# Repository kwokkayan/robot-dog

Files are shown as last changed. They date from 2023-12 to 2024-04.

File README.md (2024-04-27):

# 23/24 COMP4601 Final Year Project

## Group information

- group: fyp23005
- title: Intelligent robot design and implementation

## File Structure

- `3D_model`: STL and blender files
- `docker`: docker files for development and production environments
- `workspaces/esp32_champ_dog`: new firmware for champ
- `workspaces/newviz`: React web application for live visualizations
- `workspaces/ros/noetic`: ROS1 packages including CHAMP
- `workspaces/ros/humble`: ROS2 packages including CV utilities

## Requirements

1. `docker`, `docker-compose`, and [`docker-buildx-plugin`](https://github.com/docker/buildx)
2. Alternatively, ROS melodic to run `workspaces/ros/noetic` and ROS humble to run others.
3. `nodejs` > 21.0.0
4. Hardware requirements:
   - ESP32 microcontroller
   - MPU-9250
   - PCA9685 PWM controller
   - 12 PWM servos (MG996R, MG958, TD81XXG series...)
   - Nvidia Jetson Orin Nano Developer Kit
     - Jetpack 5.1.3
     - CUDA 11.4
   - Intel Realsense D435i

## How to run

### Firmware

1. Use PlatformIO to open `esp32_champ_dog`
2. Build and flash the firmware to `esp32`
3. Refer to `README.md` in `esp32_champ_dog` for further information.

### Development: CHAMP with ROS Melodic

1. Configure `docker-compose.yml`:
   - Web GUI Resoulution is set in `docker-compose.yml`. Please refer to [base image](https://hub.docker.com/r/dorowu/ubuntu-desktop-lxde-vnc/) for detailed configuration.
   - Pass device files to the container in `docker-compose.yml` under `device`:
     - joystick: e.g. `/dev/input/js0:/dev/input/js`
     - rfcomm socket: e.g. `/dev/rfcomm1:/dev/ttyUSB0`
     - usb socket: e.g. `/dev/ttyUSB0:/dev/ttyUSB0`
   - The following ports are opened:
     - 22: ssh
     - 5900: vnc
     - 6080: vnc
     - 9090: websocket
     - 11311, 11411: ros serial TCP socket
   - Uncomment `bind volumne` for live development
2. Run `docker-compose up -d`.
   - Use `http://localhost:6080` to access the web GUI.
   - CHAMP and other packages is installed and built
3. Refer to `README.md` in `workspaces/ros/noetic` for further information.

### Development: React webapp

1. `cd workspaces/newviz`
2. `npm i`: install dependencies
3. Configure `.env`:
   - VITE_ROS_PACKAGE=public
   - VITE_URDF_PATH=public/quadruped.urdf
   - VITE_WS_URL=`websocket url for middleware`
   - VITE_CAMERA_STREAM_URL=`http url for video stream`
4. `npm run dev`: start web server
5. Refer to `README.md` in `workspaces/newviz` for further information.

### Production environments

Start the docker container for running ROS noetic packages

```bash
$ cd docker/
$ ./build.sh noetic
$ ./run.sh noetic
> roslaunch test_config bringup.launch
```

Start the docker container for running ROS1-to-ROS2 bridge

```bash
$ cd docker/
$ ./build.sh bridge
$ ./run.sh bridge
> ros2 run ros1_bridge dynamic_bridge 2>/dev/null
```

Start the docker container for running ROS humble packages (Note that the building process of ROS packages is started after starting the container as host CUDA library are required)

```bash
$ cd docker/
$ ./build.sh humble
$ ./run.sh humble
> source /opt/ros/humble/setup.bash && colcon build --symlink-install
> source install/setup.bash && ros2 launch nvblox_examples_bringup realsense_nav2_example.launch.py
```

Start the docker container for running the web dashboard (Please refer to the `README.md` in `workspaces/newviz` for getting a Firebase API key)

```bash
$ vim workspaces/newviz/.env # To configure VITE_FIREBASE_API_KEY
$ cd docker/
$ ./build.sh newviz
$ docker run --rm -p 127.0.0.1:8080:80 ros_custom-newviz-$(uname -m)
```

Then, you can access the web dashboard at `http://127.0.0.1:8080/`.

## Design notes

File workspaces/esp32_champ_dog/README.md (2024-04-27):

# ESP32_CHAMP_DOG
## File Structure
- `include`: header files and macro configs
    - `Config.h`: choose the protocol for ROS serial (Wifi, Bluetooth SSP, and Serial are available)
- `lib`: custom libraries
    - `mpu_9250`: IMU wrapper class
    - `pwm_servo`: PWM servo wrapper class
        - `pwm_servo_offset.h`: put joint offsets after calibration here
- `src`: main files
    - `BluetoothSerial.cpp`: configure TX/RX queue sizes
    - `main.cpp`: main firmware
## How to run
1. Choose the protocol used in `Config.h`:
    - Uncomment `#define ENABLE_WIFI` to enable wifi
    - Uncomment `#define USE_BLUETOOTH` to enable bluetooth
    - Comment both to use Serial
2. Configure ros serial buffers (`ros.h`)and bluetooth buffers (`BluetoothSerial.cpp`)
3. Using Platform IO, build and flash.
4. Calibrate joints using calibration mode and adjust offsets in `pwm_servo_offset.h`
## Dependencies
- `frankjoshua/Rosserial Arduino Library@^0.9.1`
- `adafruit/Adafruit PWM Servo Driver Library@^3.0.1`
- `Wire`
- `SPI`
- `kwokkayan/SparkFun MPU-9250 Digital Motion Processing (DMP) Arduino Library (For ESP32)@^1.0.1`: forked from [here](https://github.com/sparkfun/SparkFun_MPU-9250-DMP_Arduino_Library)
## Bluetooth commands
- `sudo hcitool cc <MAC>`
- `sudo hcitool auth <MAC>`
- `sudo rfcomm bind rfcomm1 <MAC>`
- `sudo rfcomm connect /dev/rfcomm1 <MAC> 1`
## How to get absoulte orientation
1. Before powering on, face the robot to the EAST to calibrate to ENU coordinates.

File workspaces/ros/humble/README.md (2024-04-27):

# ROS Humble packages

## File Structure

- `imu_tools`: provides madgwick filter to fuse IMU sensor data into an orientation
- `isaac_ros_common`: provides common packages and utilities in Isaac ROS
- `isaac_ros_image_segmentation`: provides image segmentation packages
- `isaac_ros_nvblox`: provides Nvblox, a 3D scene reconstruction package
- `isaac_ros_object_detection`: provides object detection packages (e.g., YOLO)
- `m-explore`: provides frontier exploration and map merging packages
- `pose_estimation_filter`: provides human pose estimation package for dynamic object following
- `realsense-ros`: provides ROS wrapper for Intel RealSense camera

## How to run

- Base mode: `ros2 launch nvblox_examples_bringup realsense_nav2_example.launch.py`
- Run frontier exploration node: `ros2 launch explore_lite explore.launch.py`
- Run dynamic object following node: `ros2 run pose_estimation_filter evaluator`
  - Please see [isaac_ros_unet - Quickstart](https://nvidia-isaac-ros.github.io/repositories_and_packages/isaac_ros_image_segmentation/isaac_ros_unet/index.html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) to configure and start the image segmentation node

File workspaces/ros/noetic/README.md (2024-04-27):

# ROS Noetic packages

## File Structure

- `champ*`: CHAMP files, refer to [here](https://github.com/chvmp/champ) for instructions.
- `champ_setup_assistant`: refer to [here](https://github.com/chvmp/champ_setup_assistant) for instructions.
- `champ_teleop`: refer [here](https://github.com/chvmp/champ_teleop) for instructions.
- `esp32_ros_confollers`: `ros_control` package for esp32 hardware.
- `realsense2_description`: URDF and meshs for Intel realsense cameras.
- `test_config`: main config for robot:
  - `urdf`: URDF files and meshes for the robot
  - `config`: configuration files for gait, pid, ...
  - `launch`: launch files

## How to run

- Joint calibration mode: `roslaunch test_config bringup.launch rviz:=true hardware_connected:=true publish_joint_control:=false calibrate_joints:=true balance_mode:=false`
- Hardware connected without balance mode: `roslaunch test_config bringup.launch hardware_connected:=true balance_mode:=false`
- Hardware connected with balance mode: `roslaunch test_config bringup.launch hardware_connected:=true`
- Hardware connected (TCP protocol) with balance mode: `roslaunch test_config bringup.launch hardware_connected:=true ros_serial_tcp:=true`
- Hardware connected with custom baud rate and device file: `roslaunch test_config bringup.launch hardware_connected:=true baud_rate:=1000000 device_file:=/dev/ttyUSB0`
- Joystick control:`roslaunch champ_teleop teleop.launch joy:=true`
- Refer to CHAMP for other commands

## Configuration

- Balance Mode pid: go to `src/test_config/config/pid/pid.yaml`
- Gait config: go to `src/test_config/config/gait/gait.yaml`

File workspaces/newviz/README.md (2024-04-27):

# NEWVIZ

## Prerequisite

1. Google account (for creating Firebase projects)

## Configuration

Configure [environement file] (.env):

- VITE_ROS_PACKAGE=public
- VITE_URDF_PATH=public/quadruped.urdf
- VITE_WS_URL= Websocket URL for ROS connection
- VITE_CAMERA_STREAM_URL= URL for live camera stream
- VITE_FIREBASE_API_KEY = API key of your firebase project

## Launch the Web

1. run shell command to install dependencies\
   `npm i`
2. run shell command to start web server\
   `npm run dev`

## How to get the API key

1. Visit [Firebase](https://firebase.google.com/) and go to console
2. Create a new Firebase project
3. Go to Project Setting and create a web app
4. Firebase will generate API key, appId for you
5. Replace the codes in firebase.js with your web app's Firebase configuration
   (See [Add Firebase to your JavaScript project](https://firebase.google.com/docs/web/setup#add_firebase_to_your_app) )

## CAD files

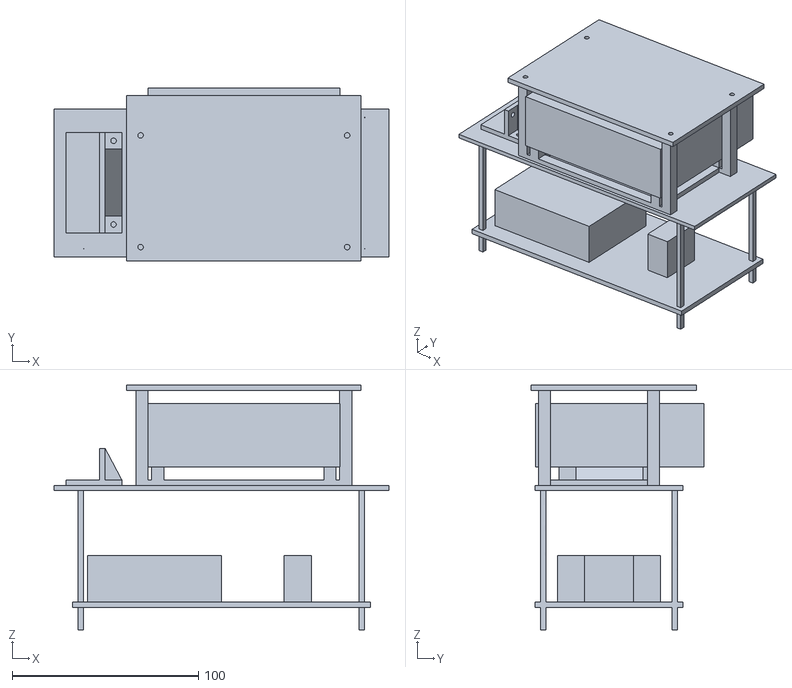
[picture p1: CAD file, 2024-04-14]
3D_model/stl_models/tower.stl
180.0 x 93.0 x 131.5

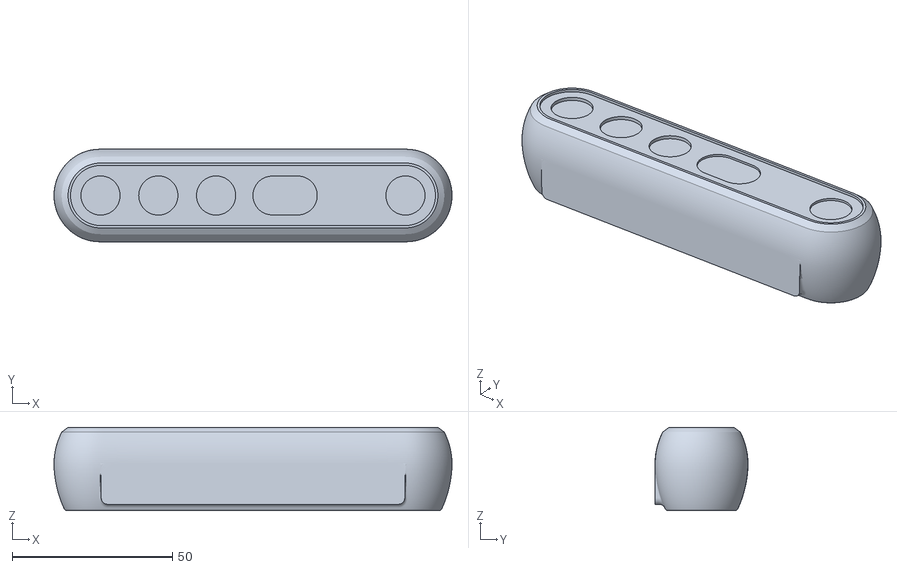
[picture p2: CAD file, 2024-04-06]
workspaces/newviz/public/realsense2_description/meshes/d455.stl
124.0 x 29.0 x 26.0

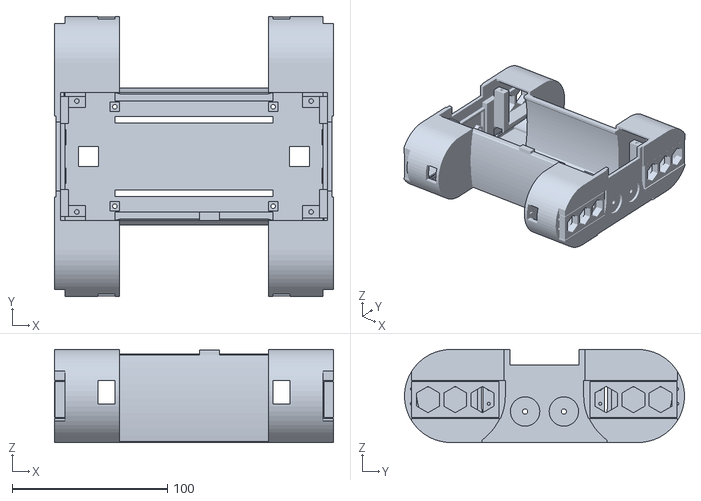
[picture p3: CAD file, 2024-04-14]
workspaces/newviz/public/test_config/meshes/base.stl
180.0 x 180.5 x 60.0

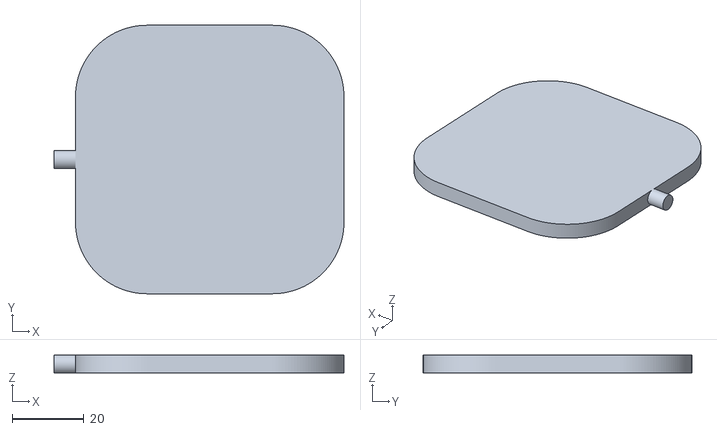
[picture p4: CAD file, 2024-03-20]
workspaces/ros/noetic/champ_description/meshes/arm/wrist2.stl
81.0 x 75.0 x 5.00

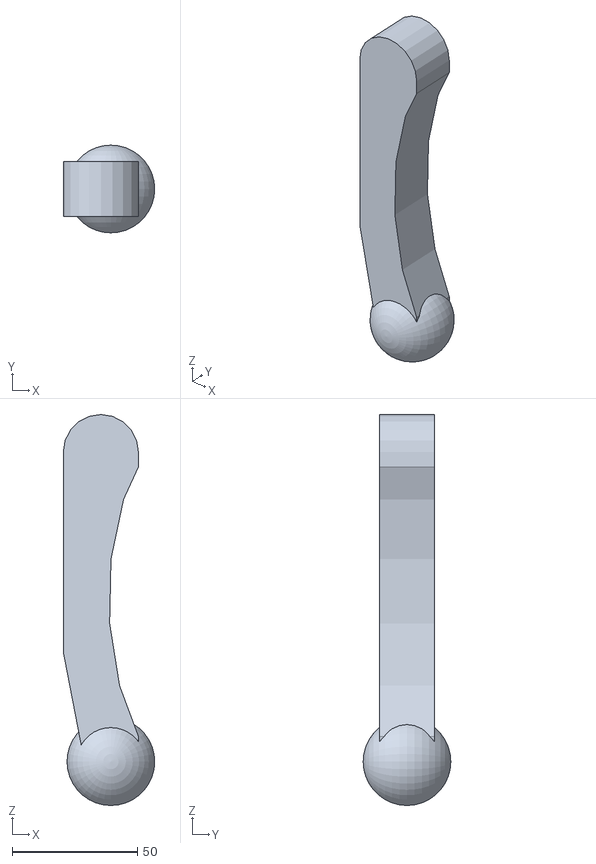
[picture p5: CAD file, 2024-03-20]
workspaces/ros/noetic/champ_description/meshes/lower_leg.stl
36.5 x 35.0 x 156.0

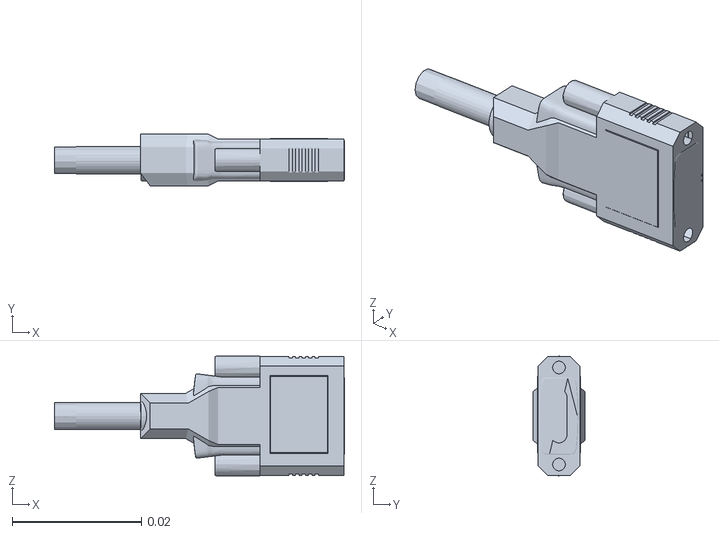
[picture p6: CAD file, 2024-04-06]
workspaces/ros/noetic/realsense2_description/meshes/plug.stl
0.0448 x 0.008 x 0.0185

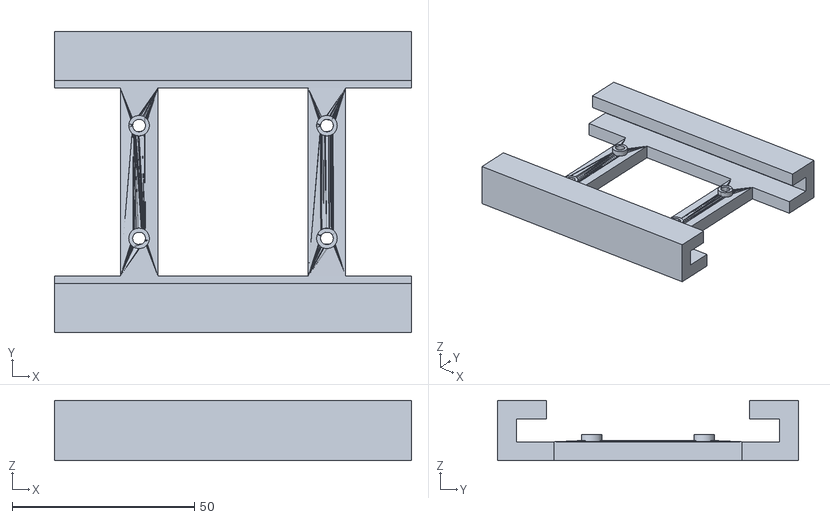
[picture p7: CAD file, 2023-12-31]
3D_model/stl_models/refined_sbc_header.stl
97.8 x 82.4 x 16.5

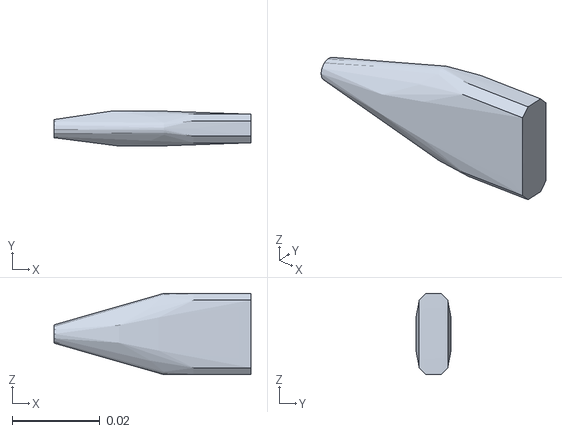
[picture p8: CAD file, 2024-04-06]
workspaces/newviz/public/realsense2_description/meshes/plug_collision.stl
0.0448 x 0.008 x 0.0185

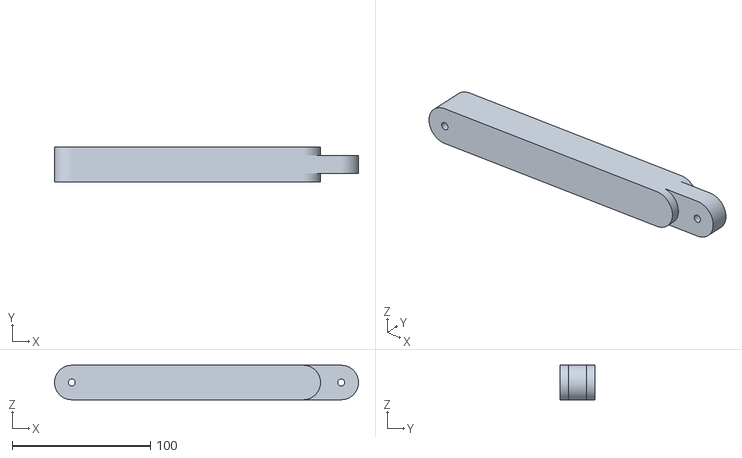
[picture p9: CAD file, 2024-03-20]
workspaces/ros/noetic/champ_description/meshes/arm/lower_arm.stl
220.0 x 25.0 x 25.0

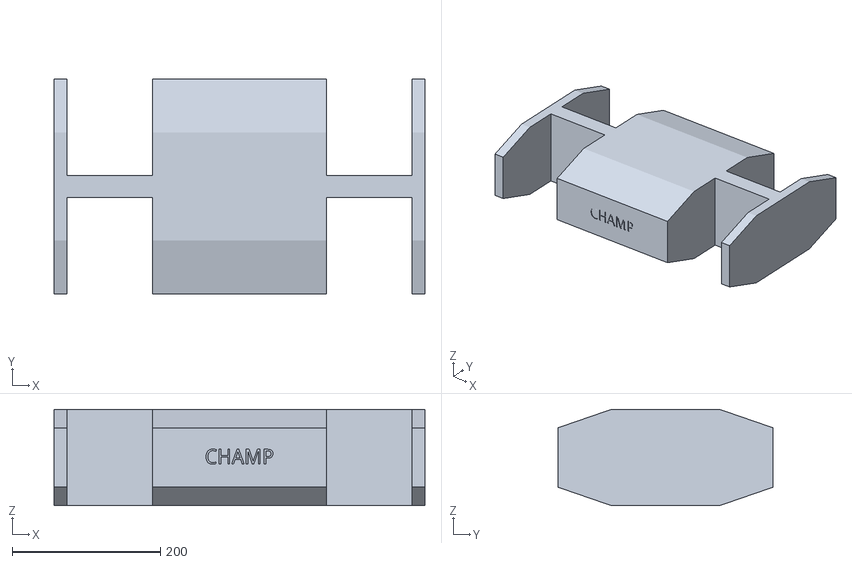
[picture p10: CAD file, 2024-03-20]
workspaces/ros/noetic/champ_description/meshes/base.stl
500.0 x 290.0 x 130.0

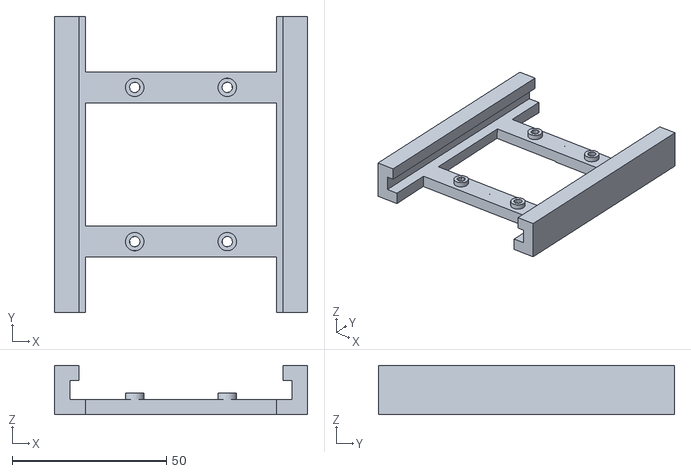
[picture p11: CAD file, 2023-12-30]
3D_model/stl_models/small_sbc_header.stl
82.0 x 96.0 x 16.0

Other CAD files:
workspaces/newviz/public/test_config/meshes/tower.stl
workspaces/ros/noetic/test_config/meshes/tower.stl
3D_model/blends/base.blend
3D_model/blends/bumper.blend
3D_model/blends/foot.blend
3D_model/blends/hip.blend
3D_model/blends/lower-leg.blend
3D_model/blends/tower.blend
3D_model/blends/upper-leg.blend
3D_model/stl_models/body-bottom.stl
3D_model/stl_models/body-bumper.stl
3D_model/stl_models/body-top.stl
3D_model/stl_models/lower-joint_foot_left.stl
3D_model/stl_models/lower-joint_foot_right.stl
3D_model/stl_models/lower-joint_left_leg.stl
3D_model/stl_models/lower-joint_right_leg.stl
3D_model/stl_models/servo-arm-extension.stl
3D_model/stl_models/shoulder_join_left.stl
3D_model/stl_models/shoulder_join_right.stl
3D_model/stl_models/triangular_ruler.stl
3D_model/stl_models/upper-joint_left1.stl
3D_model/stl_models/upper-joint_left2.stl
3D_model/stl_models/upper-joint_right1.stl
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

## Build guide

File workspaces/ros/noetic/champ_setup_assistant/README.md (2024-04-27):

# CHAMP Setup Assistant  
This software auto generates a configuration package containing all the [files](https://github.com/chvmp/champ_setup_assistant/tree/master/templates) necessary to make CHAMP walk. 

CHAMP Setup Assistant
## 1. Installation

### 1.1. Clone and install all dependencies:

        sudo apt install -y python-rosdep
        cd <your_ws>/src
        git clone https://github.com/chvmp/champ_setup_assistant
        cd ..
        rosdep install --from-paths src --ignore-src -r -y

### 1.2.  Build your workspace:

        cd <your_ws>
        catkin_make
        source <your_ws/>/devel/setup.bash

## 2. Quick Start

### 2.1. Run the setup assistant:

        roslaunch champ_setup_assistant setup_assistant.launch 

Configure your robot by loading a URDF or manually key in the configuration parameters. If you don't have a URDF now, you can download [ANYmal](https://github.com/chvmp/anymal_b_simple_description/tree/master/urdf) or [SpotMicro](https://github.com/chvmp/spotmicro_description/blob/master/urdf/spotmicroai.urdf) to try the package.

## 3. Leg Configuration

You can either use a URDF file or manually key in the origin of each actuator in the robot.

### 3.1. Using a URDF file:

 3.1.1 The following assumptions have been made to avoid fragmentation across different robots as there can be thousands of ways to create a robot's URDF. You need to modify your URDF if any of these assumptions are not met:

- There are no rotation between frames (joint's origin-rpy are all set to zero).
- Hip joints rotate in the X axis.
- Upper Leg joints rotate in the Y axis.
- Lower Leg joints rotate in the Y axis.
- Origins of actuators' meshes are located at the center of rotation.
- All joints at zero position will results the robot's legs to be fully stretched towards the ground. From frontal and sagittal view, all legs should be perpendicular to the ground.

You can use the image below as a reference.

AXES: +X: Red, +Y: Green, +Z: Blue 
  CHAMP Setup Assistant

3.1.2 Load the URDF file:
   
- Click the 'BROWSE URDF' button on the upper right corner and click the URDF file you want to use from the file browser. Double click the file or click 'Open' to load the URDF.

- Click the 'LOAD' button. This will list down the links of the robot on the left pane and display the robot's meshes on the RVIZ widget. Take note that it may take a while for huge mesh files to load.

    CHAMP Setup Assistant

3.1.3 Select the namespace for each leg (auto-configuration):
   
- Select the correct namespace for each leg on the drop-down menu. 

  CHAMP Setup Assistant

  This namespace is the unique identifier used by the URDF's author to differentiate each leg. For instance, Anymal's hip links are named as LF_HIP (front left), LH_HIP (rear left), RF_HIP (right front), RH_HIP (rear right). The assistant will parse the namespaces as LF_, LH_, RF_, and RH_. After selecting the namespaces for all the legs, the assistant will automatically drag the links to its respective leg parts, emptying the left pane.

3.1.4 Manually adding links if auto-configuration in previous step (3.1.2) fails:

- You can also add a link to each leg part manually by clicking on a leg tab (ie 'Left Front Leg'). Select a link on the left pane and click '>' to add. This would be useful if the assistant fails to parse the namespaces.
   
  CHAMP Setup Assistant

3.1.5 Verify the configuration:

- To visualize a configured link for a leg part, click on one of the leg tabs (ie 'Left Front Leg') and select the part. The link should now be highlighted on the RVIZ widget. Check all the leg tabs if the configuration is correct.

  CHAMP Setup Assistant

### 3.2. Manual Joint Configuration:

This step is only required if you don't have a URDF file to use. In this step, you'll define the position of each actuator in your robot to help the controller find the relative position of each joints.

- Click the 'Left Front Leg' tab and key in the position for each actuator. When defining an actuator's position, x, y, and z refers to:

  x: Translation in the x axis from a reference frame. + x to the front, -x to the back.

  y: Translation in the y axis from a reference frame. + y to the left, -y to the right.

  z: Translation in the z axis from a reference frame. + z up, -z down.

By reference frame, it means the previous part in this chain: base - hip - upper_leg - lower_leg - foot. For instance if you're defining the position of the actuator at the hip, the reference frame will be 'base' and if youre defining the position of the upper_leg then your reference frame will be 'hip'.  

You can take a look at the diagram below to gain some intuition. Alway define these positions from a bird's eye view.
   
CHAMP Setup Assistant

Some axis won't allow you to define in a certain direction if the assistant thinks that it doesn't make sense to define the position towards that direction. For instance, you won't be able to define front right hip's actuator y value as positive as this actuator is always at the right side (-y) of the base.

Once you're done with the left-front leg, the assistant will somehow predict the rest of the actuators' position. You can click on the rest of the leg tabs to check if the predictions are correct. You can still define the position manually if the prediction is wrong.

## 4. Gait Configuration

Click on the 'Gait Configuration' tab to define the robot's walking parameters.

CHAMP Setup Assistant

  - **Knee Orientation** - How the knees should be bent. You can can configure the robot to follow the following orientation .>> .>< .<< .<> where dot is the front side of the robot.

  - **Max Linear Velocity X** (meters/second) - Robot's maximum forward/reverse speed.

  - **Max Linear Velocity Y** (meteres/second) - Robot's maximum speed when moving sideways.

  - **Max Angular Velocity Z** (radians/second)- Robot's maximum rotational speed.

  - **Stance Duration** (seconds)- How long should each leg spend on the ground while walking. You can set this to default(0.25) if you're not sure. The higher the stance duration the further the displacement is from the reference point.

  - **Leg Swing Height** (meters)- Trajectory height during swing phase.

  - **Leg Stance Height** (meters)- Trajectory depth during stance phase.

  - **Robot Walking Height** (meters) - Distance from hip to the ground while walking. Take note that setting this parameter too high can get your robot unstable.

  - **CoM X Translation** (meters) - You can use this parameter to move the reference point in the X axis. This is useful when you want to compensate for the weight if the center of mass is not in the middle of the robot (from front hip to rear hip). For instance, if you find that the robot is heavier at the back, you'll set a negative value to shift the reference point to the back.

  - **Odometry Scaler** - You can use this parameter as a multiplier to the calculated velocities for dead reckoning. This can be useful to compensate odometry errors on open-loop systems. Normally this value ranges from 1.0 to 1.20.
  
## 5. Generate Config Package

  Before you generate the configuration package make sure you have configured all the legs and set the correct gait configurations.

- Click the 'Generate Config' tab and key-in the robot name. 
- Click the 'Browse' button to choose the 'src' directory of your current catkin workspace.
- Click 'Generate' button to create the configuration package.

  CHAMP Setup Assistant

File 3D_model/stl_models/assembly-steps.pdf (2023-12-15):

# Assembling Step

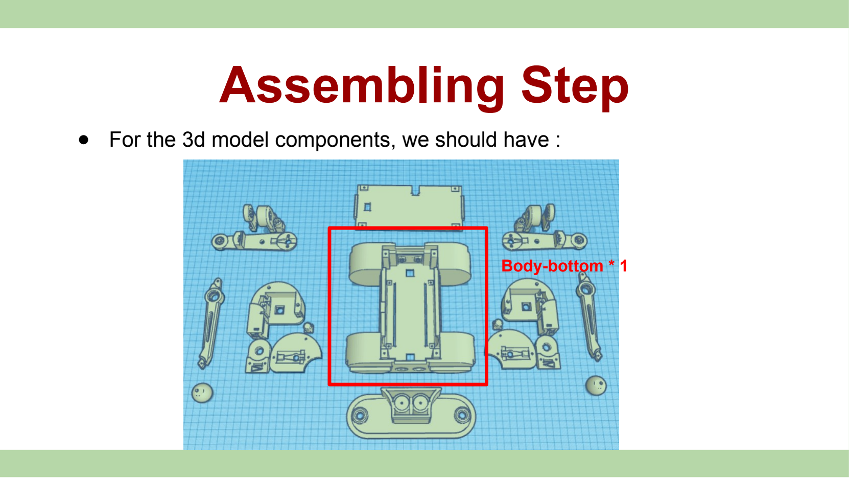
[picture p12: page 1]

- For the 3d model components, we should have :

Body-bottom * 1

Body-top * 1

Body-bumper * 2

Left-shoulder-joint * 2

Left-upper-joint * 2

Left-lower-joint * 2

Left-foot * 2

Right-shoulder-joint * 2

Right-upper-joint * 2

Right-lower-joint * 2

Right-foot * 2

# Assemble Step

- For the other components, we have :

Servo motor * 12

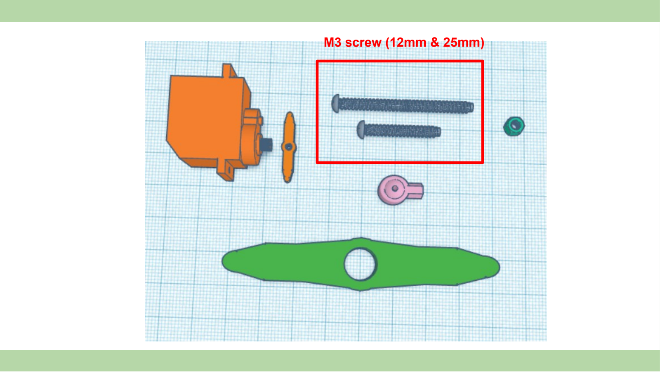
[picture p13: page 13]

M3 screw (12mm & 25mm)

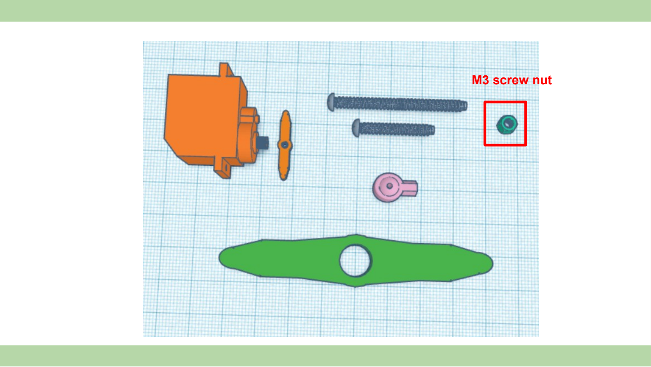
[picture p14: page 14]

M3 screw nut

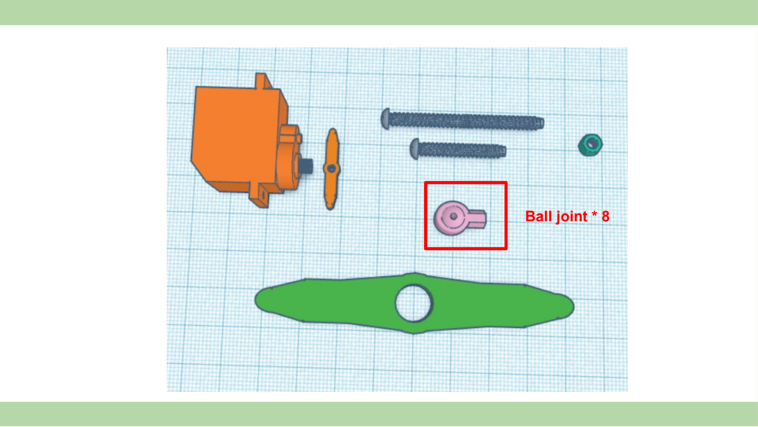
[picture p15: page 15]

Ball joint * 8

Lower-joint-servo-gear * 4

- First we need to cut the M3 screw and put ball joint at its two end
- Repeat four times, make sure they have the same length

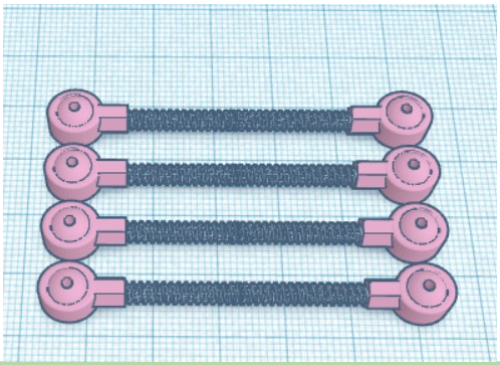
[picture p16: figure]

- Next, we work on the body part
- Screw the the body with the servos on each shoulder

- Then we connect the foot (right) and the lower joint (right)
- Screw them together

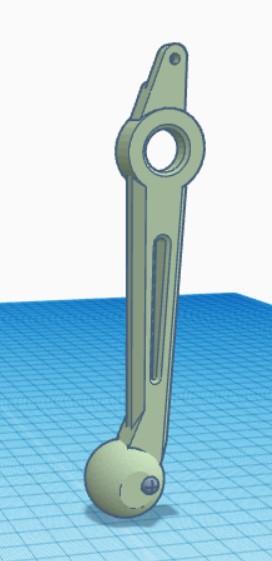
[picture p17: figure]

- Connect the lower joint (right) and the upper joint (right) together with servo motor
- Screw them together

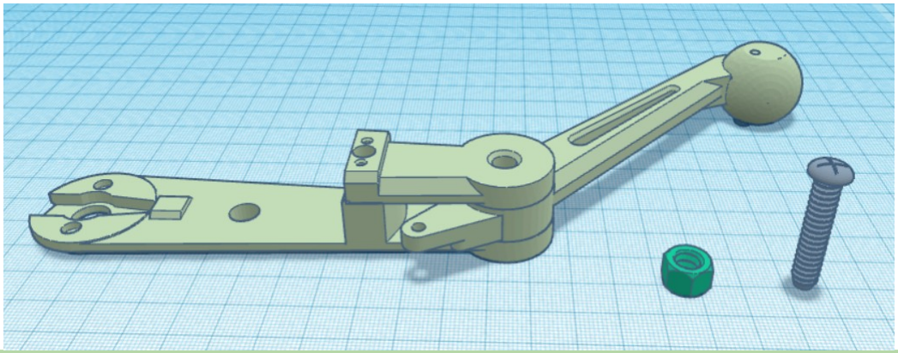
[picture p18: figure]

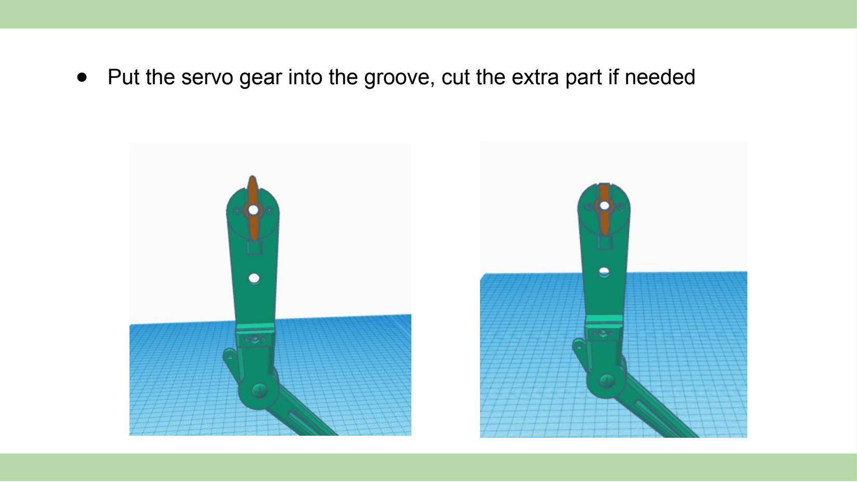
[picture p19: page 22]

- Put the servo gear into the groove, cut the extra part if needed

- Connect the remaining upper joint parts

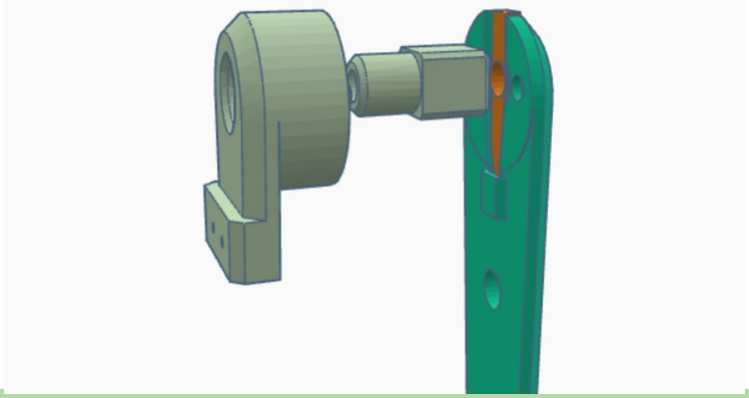
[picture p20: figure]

- Connect the remaining upper joint parts

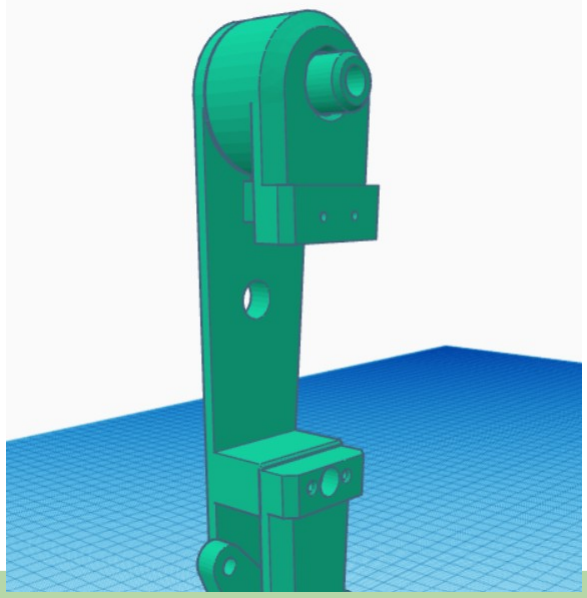
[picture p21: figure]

- Screw the servo and the upper joint

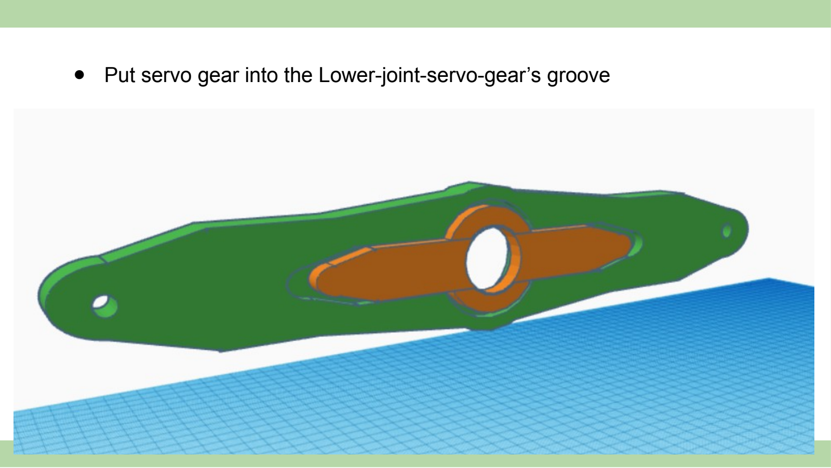
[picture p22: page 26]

- Put servo gear into the Lower-joint-servo-gear’s groove

- Connect the lower-joint-servo-gear to the servo motor

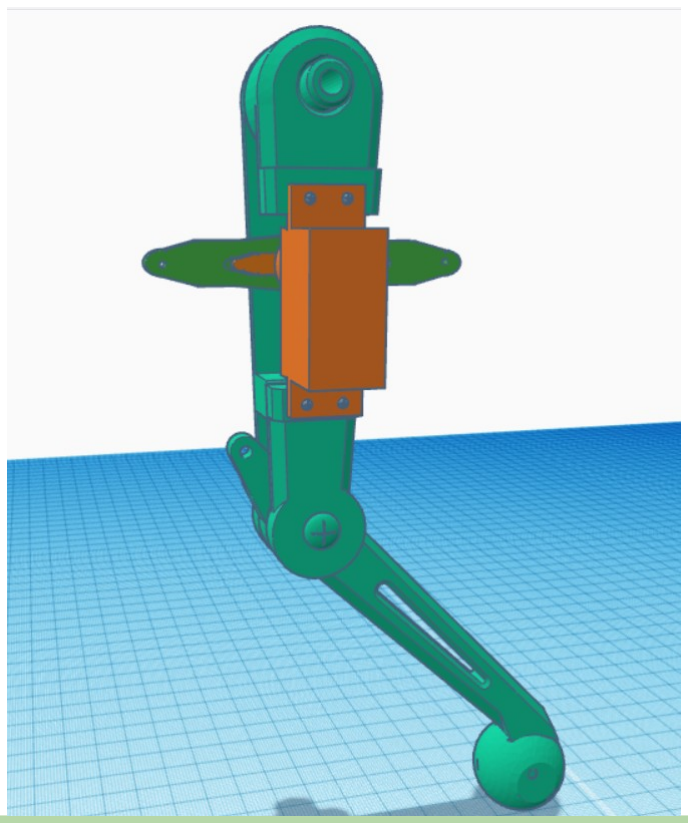
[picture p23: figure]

- Screw the ball joint with the lower-joint-servo-gear and lower joint

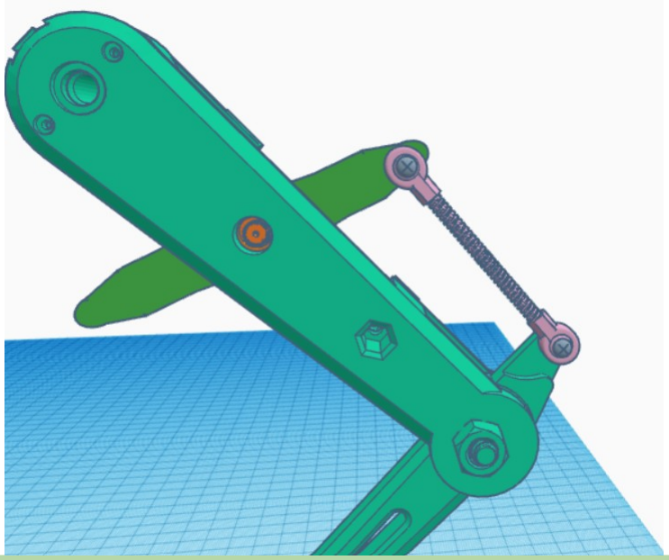
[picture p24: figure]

- Same step for the left leg

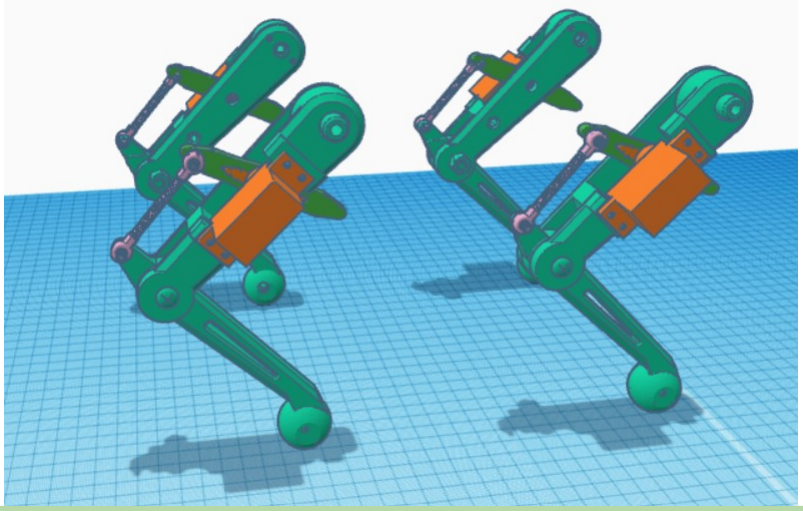
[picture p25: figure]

- After that, we work on the shoulder part (right)
- Put the servo gear into the groove, cut the extra part if needed

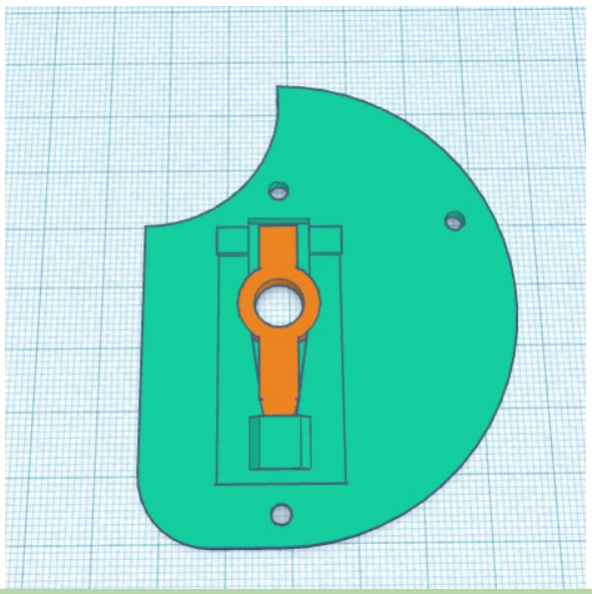
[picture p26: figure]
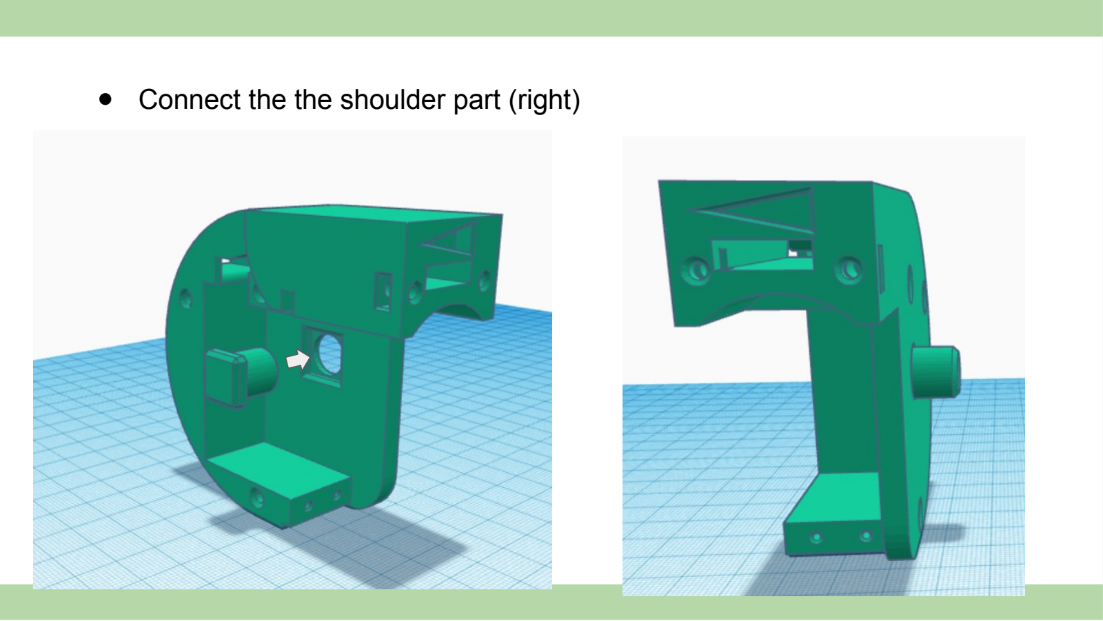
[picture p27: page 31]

- Connect the the shoulder part (right)

- Screw the servo with the shoulder (right)

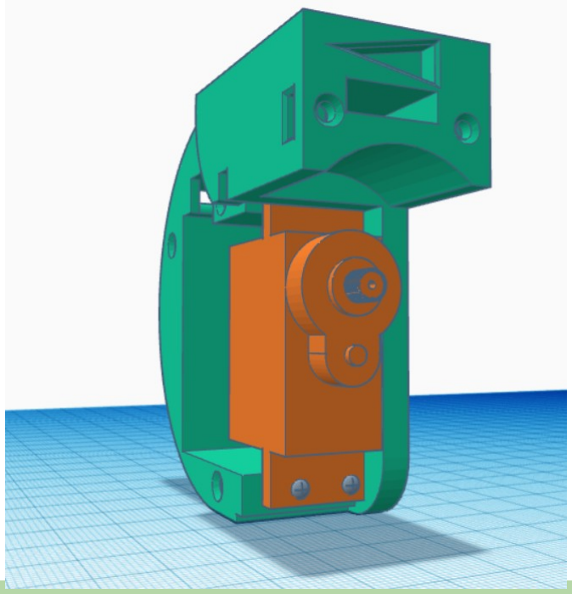
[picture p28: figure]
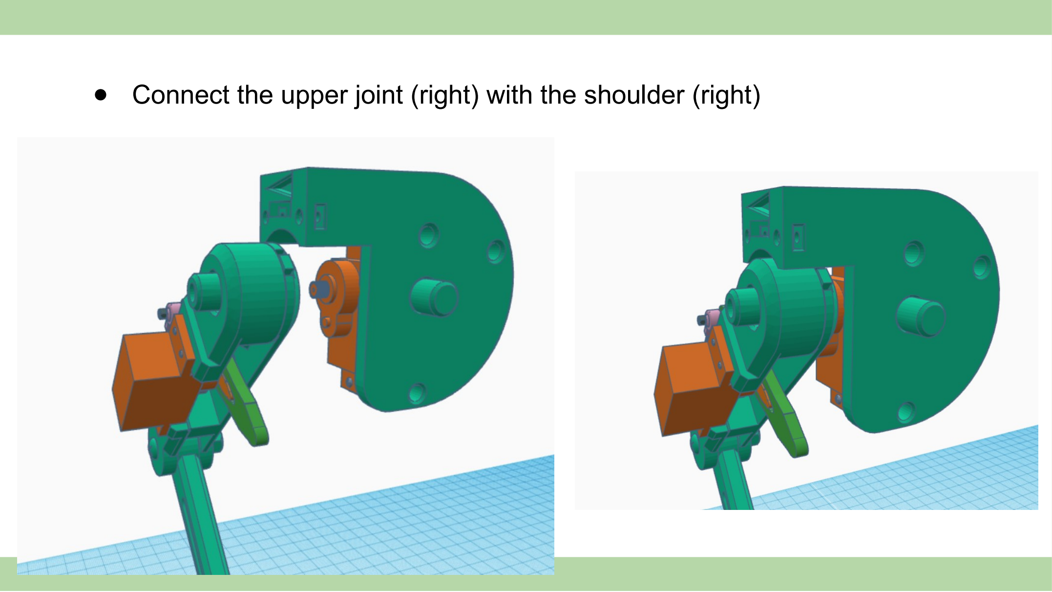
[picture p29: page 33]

- Connect the upper joint (right) with the shoulder (right)

- Connect the remaining parts of the shoulder
- Make sure the wire can pass through the hole

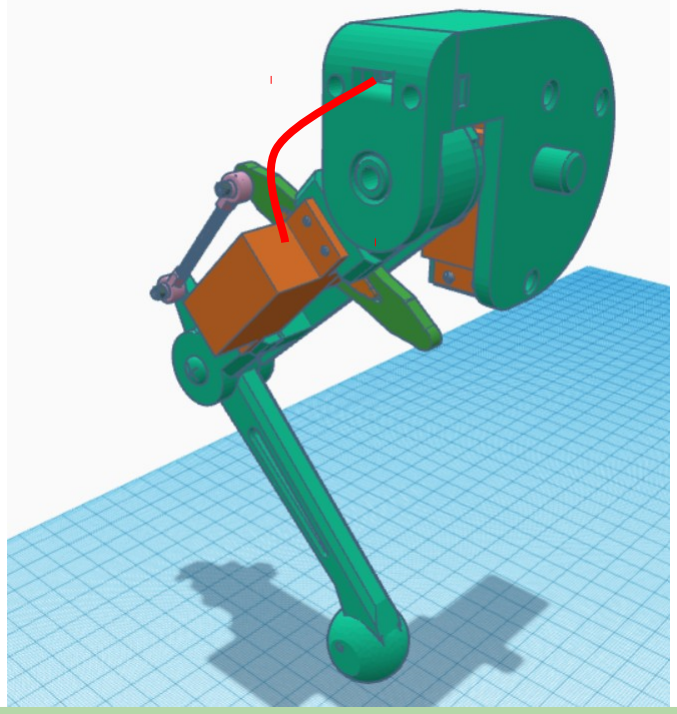
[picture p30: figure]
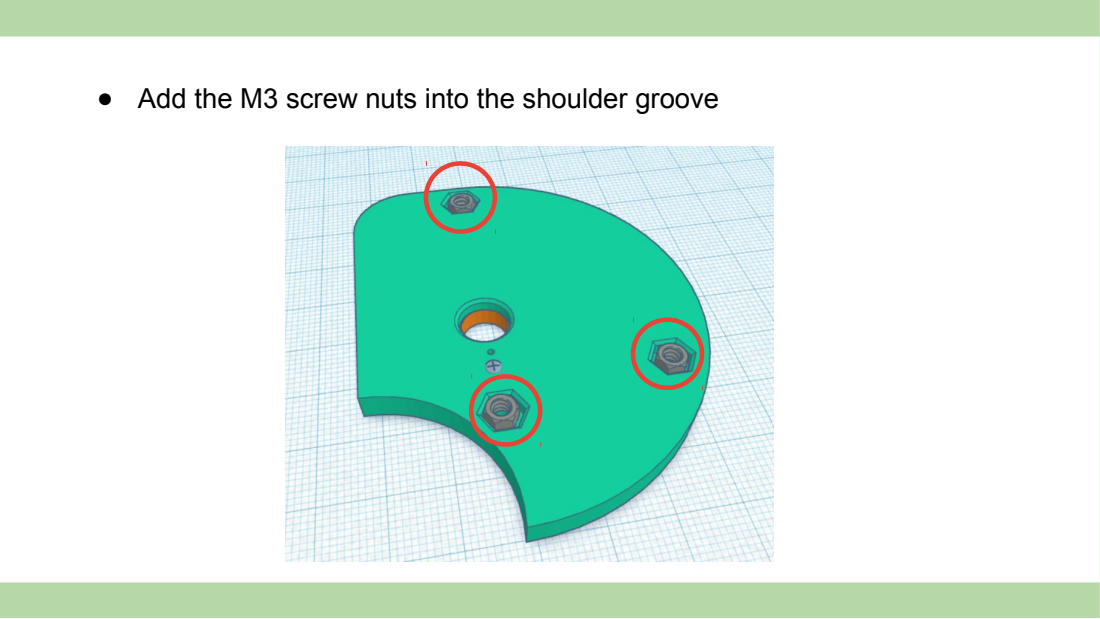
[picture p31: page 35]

● Add the M3 screw nuts into the shoulder groove

- Connect the shoulder with the body

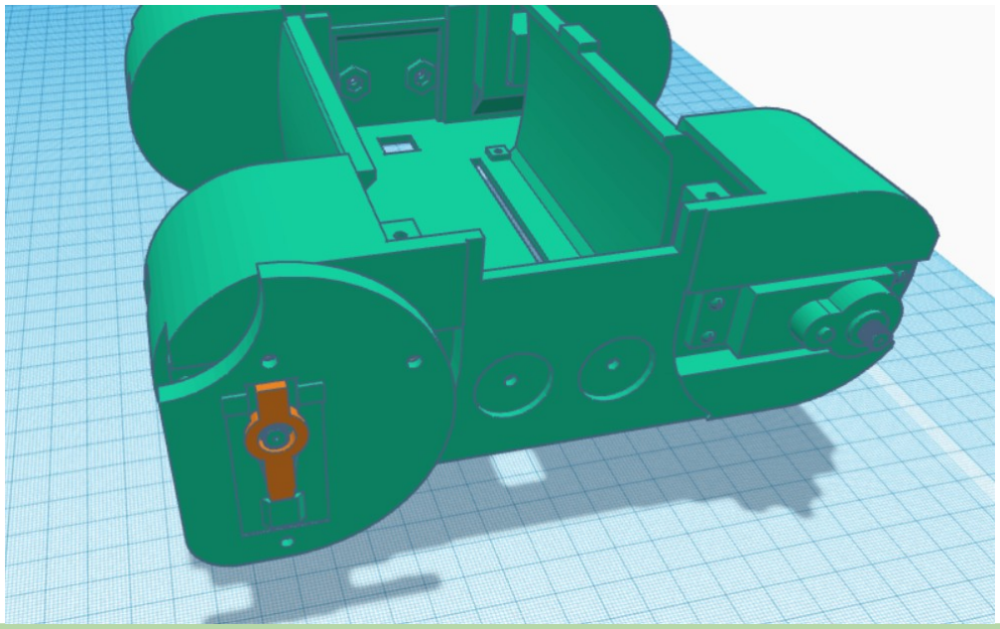
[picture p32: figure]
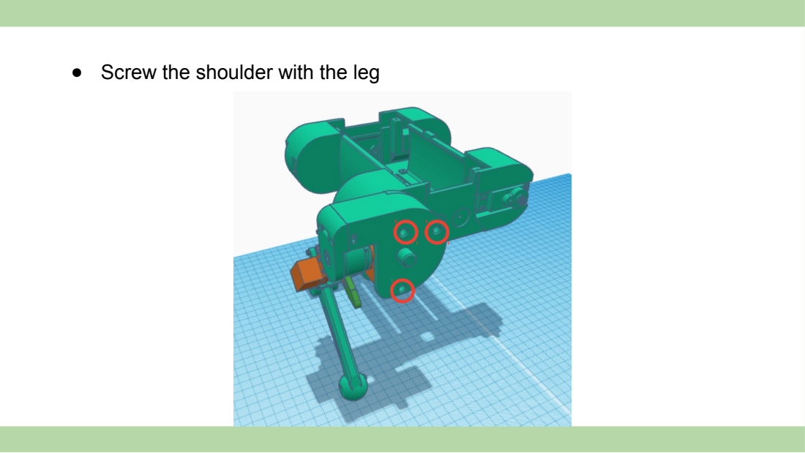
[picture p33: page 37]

● Screw the shoulder with the leg

- Repeat the same step to finish the remaining legs

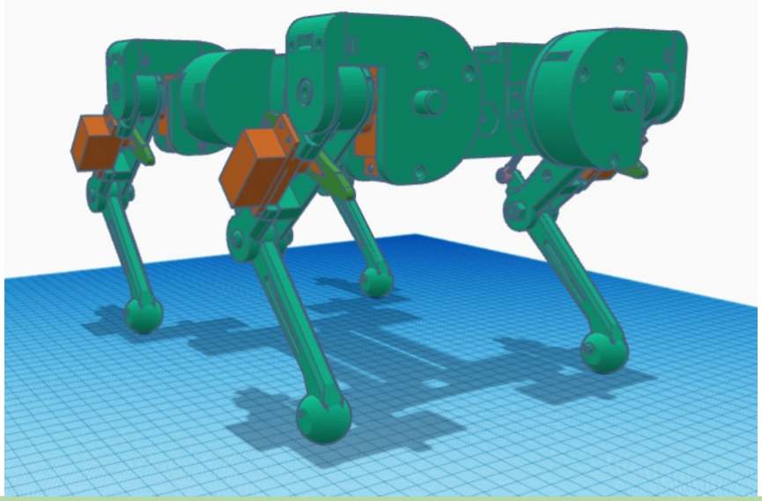
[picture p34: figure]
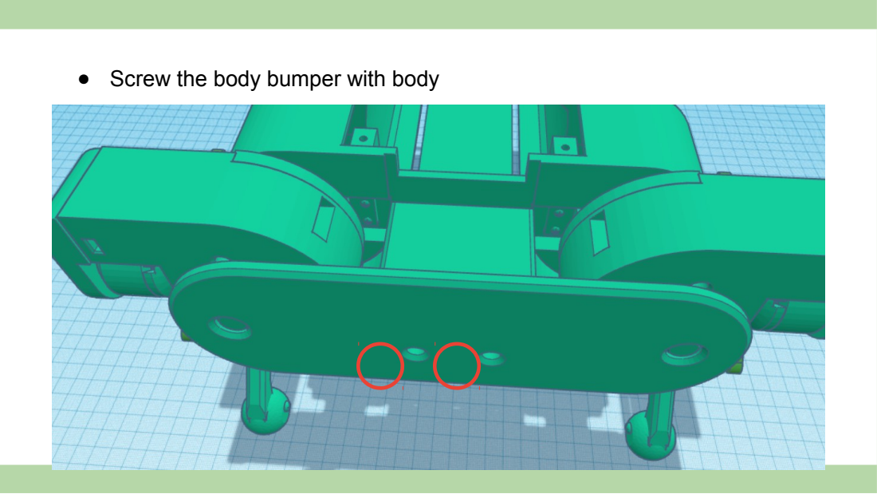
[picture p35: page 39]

● Screw the body bumper with body

- Done!

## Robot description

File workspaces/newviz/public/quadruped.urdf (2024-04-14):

<?xml version="1.0" ?>
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
<robot name="quadruped">
  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
  <link name="base_link">
    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
  </link>
  <link name="tower_link">
    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
  </link>
  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
  <joint name="camera_joint" type="fixed">
    <origin rpy="0 0 0" xyz="0.075 0 0.099"/>
    <parent link="base_link"/>
    <child link="camera_bottom_screw_frame"/>
  </joint>
  <link name="camera_bottom_screw_frame"/>
  <joint name="camera_link_joint" type="fixed">
    <origin rpy="0 0 0" xyz="0.010600000000000002 0.0175 0.0125"/>
    <parent link="camera_bottom_screw_frame"/>
    <child link="camera_link"/>
  </joint>
  <link name="camera_link">
    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
    <inertial>
      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
      <mass value="0.072"/>
      <origin xyz="0 0 0"/>
      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
    </inertial>
  </link>
  <link name="f_bumper_link">
    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
  </link>
  <link name="h_bumper_link">
    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
  </link>
  <link name="lf_hip_link">
    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
  </link>
  <link name="lf_upper_leg_link">
    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
  </link>
  <link name="lf_lower_leg_link">
    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
  </link>
  <link name="lf_foot_link">
    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
  </link>
  <link name="rf_hip_link">
    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
  </link>
  <link name="rf_upper_leg_link">
    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
  </link>
  <link name="rf_lower_leg_link">
    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
  </link>
  <link name="rf_foot_link">
    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
  </link>
  <link name="lh_hip_link">
    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
  </link>
  <link name="lh_upper_leg_link">
    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
  </link>
  <link name="lh_lower_leg_link">
    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
  </link>
  <link name="lh_foot_link">
    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
  </link>
  <link name="rh_hip_link">
    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
  </link>
  <link name="rh_upper_leg_link">
    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
  </link>
  <link name="rh_lower_leg_link">
    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
  </link>
  <link name="rh_foot_link">
    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
  </link>
  <joint name="tower_joint" type="fixed">
    <origin rpy="0 0 0" xyz="0.0056 0.0068 0.10042"/>
    <parent link="base_link"/>
    <child link="tower_link"/>
  </joint>
  <joint name="f_bumper_joint" type="fixed">
    <origin rpy="0 0 0" xyz="0.1203 0.0000 -0.0042"/>
    <parent link="base_link"/>
    <child link="f_bumper_link"/>
  </joint>
  <joint name="h_bumper_joint" type="fixed">
    <origin rpy="0 0 0" xyz="-0.1199 0.0000 -0.0042"/>
    <parent link="base_link"/>
    <child link="h_bumper_link"/>
  </joint>
  <joint name="lf_hip_joint" type="revolute">
    <origin rpy="0 0 0" xyz="0.1105 0.0716 0.0009"/>
    <parent link="base_link"/>
    <child link="lf_hip_link"/>
    <axis xyz="1 0 0"/>
    <limit effort="25" lower="-0.8726" upper="0.8726" velocity="1.5"/>
  </joint>
  <joint name="lf_upper_leg_joint" type="revolute">
    <origin rpy="0 0 0" xyz="0.0000 0.0355 0.0041"/>
    <parent link="lf_hip_link"/>
    <child link="lf_upper_leg_link"/>
    <axis xyz="0 1 0"/>
    <limit effort="25" lower="-1.0472" upper="1.0472" velocity="1.5"/>
  </joint>
  <joint name="lf_lower_leg_joint" type="revolute">
    <origin rpy="0 0 0" xyz="0.0002 0.0003 -0.1078"/>
    <parent link="lf_upper_leg_link"/>
    <child link="lf_lower_leg_link"/>
    <axis xyz="0 1 0"/>
    <limit effort="25" lower="-2.0944" upper="-1.0472" velocity="1.5"/>
  </joint>
  <joint name="lf_foot_joint" type="fixed">
    <origin rpy="0 0 0" xyz="-0.0093 -0.0003 -0.1060"/>
    <parent link="lf_lower_leg_link"/>
    <child link="lf_foot_link"/>
  </joint>
  <joint name="rf_hip_joint" type="revolute">
    <origin rpy="0 0 0" xyz="0.1105 -0.0716 0.0009"/>
    <parent link="base_link"/>
    <child link="rf_hip_link"/>
    <axis xyz="1 0 0"/>
    <limit effort="25" lower="-0.8726" upper="0.8726" velocity="1.5"/>
  </joint>
  <joint name="rf_upper_leg_joint" type="revolute">
    <origin rpy="0 0 0" xyz="0.0000 -0.0355 0.0041"/>
    <parent link="rf_hip_link"/>
    <child link="rf_upper_leg_link"/>
    <axis xyz="0 1 0"/>
    <limit effort="25" lower="-1.0472" upper="1.0472" velocity="1.5"/>
  </joint>
  <joint name="rf_lower_leg_joint" type="revolute">
    <origin rpy="0 0 0" xyz="0.0002 -0.0003 -0.1078"/>
    <parent link="rf_upper_leg_link"/>
    <child link="rf_lower_leg_link"/>
    <axis xyz="0 1 0"/>
    <limit effort="25" lower="-2.0944" upper="-1.0472" velocity="1.5"/>
  </joint>
  <joint name="rf_foot_joint" type="fixed">
    <origin rpy="0 0 0" xyz="-0.0093 -0.0003 -0.1060"/>
    <parent link="rf_lower_leg_link"/>
    <child link="rf_foot_link"/>
  </joint>
  <joint name="lh_hip_joint" type="revolute">
    <origin rpy="0 0 0" xyz="-0.1131 0.0716 0.0009"/>
    <parent link="base_link"/>
    <child link="lh_hip_link"/>
    <axis xyz="1 0 0"/>
    <limit effort="25" lower="-0.8726" upper="0.8726" velocity="1.5"/>
  </joint>
  <joint name="lh_upper_leg_joint" type="revolute">
    <origin rpy="0 0 0" xyz="0.0000 0.0355 0.0041"/>
    <parent link="lh_hip_link"/>
    <child link="lh_upper_leg_link"/>
    <axis xyz="0 1 0"/>
    <limit effort="25" lower="-1.0472" upper="1.0472" velocity="1.5"/>
  </joint>
  <joint name="lh_lower_leg_joint" type="revolute">
    <origin rpy="0 0 0" xyz="0.0002 0.0003 -0.1078"/>
    <parent link="lh_upper_leg_link"/>
    <child link="lh_lower_leg_link"/>
    <axis xyz="0 1 0"/>
    <limit effort="25" lower="-2.0944" upper="-1.0472" velocity="1.5"/>
  </joint>
  <joint name="lh_foot_joint" type="fixed">
    <origin rpy="0 0 0" xyz="-0.0093 -0.0003 -0.1060"/>
    <parent link="lh_lower_leg_link"/>
    <child link="lh_foot_link"/>
  </joint>
  <joint name="rh_hip_joint" type="revolute">
    <origin rpy="0 0 0" xyz="-0.1131 -0.0716 0.0009"/>
    <parent link="base_link"/>
    <child link="rh_hip_link"/>
    <axis xyz="1 0 0"/>
    <limit effort="25" lower="-0.8726" upper="0.8726" velocity="1.5"/>
  </joint>
  <joint name="rh_upper_leg_joint" type="revolute">
    <origin rpy="0 0 0" xyz="0.0000 -0.0355 0.0041"/>
    <parent link="rh_hip_link"/>
    <child link="rh_upper_leg_link"/>
    <axis xyz="0 1 0"/>
    <limit effort="25" lower="-1.0472" upper="1.0472" velocity="1.5"/>
  </joint>
  <joint name="rh_lower_leg_joint" type="revolute">
    <origin rpy="0 0 0" xyz="0.0002 -0.0003 -0.1078"/>
    <parent link="rh_upper_leg_link"/>
    <child link="rh_lower_leg_link"/>
    <axis xyz="0 1 0"/>
    <limit effort="25" lower="-2.0944" upper="-1.0472" velocity="1.5"/>
  </joint>
  <joint name="rh_foot_joint" type="fixed">
    <origin rpy="0 0 0" xyz="-0.0093 -0.0003 -0.1060"/>
    <parent link="rh_lower_leg_link"/>
    <child link="rh_foot_link"/>
  </joint>
</robot>

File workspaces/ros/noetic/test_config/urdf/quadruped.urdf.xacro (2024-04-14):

<?xml version="1.0" ?>
<robot name="quadruped" xmlns:xacro="http://www.ros.org/wiki/xacro">
    <xacro:arg name="use_nominal_extrinsics" default="false" />
     <xacro:include filename="$(find realsense2_description)/urdf/_d435i.urdf.xacro"/>
    <link name="base_link">
        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
    </link>
    <link name="tower_link">
        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
    </link>
    <xacro:sensor_d435i parent="base_link" use_nominal_extrinsics="$(arg use_nominal_extrinsics)">
        <origin xyz="0.075 0 0.099" rpy="0 0 0"/>
    </xacro:sensor_d435i>
    <link name="f_bumper_link">
        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
    </link>
    <link name="h_bumper_link">
        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
    </link>
    <link name="lf_hip_link">
        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
    </link>
    <link name="lf_upper_leg_link">
        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
    </link>
    <link name="lf_lower_leg_link">
        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
    </link>
    <link name="lf_foot_link">
        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
    </link>
    <link name="rf_hip_link">
        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
    </link>
    <link name="rf_upper_leg_link">
        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
    </link>
    <link name="rf_lower_leg_link">
        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
    </link>
    <link name="rf_foot_link">
        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 
    </link>
    <link name="lh_hip_link">
        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
    </link>
    <link name="lh_upper_leg_link">
        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
    </link>
    <link name="lh_lower_leg_link">
        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
    </link>
    <link name="lh_foot_link">
        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
    </link>
    <link name="rh_hip_link">
        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
    </link>
    <link name="rh_upper_leg_link">
        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
    </link>
    <link name="rh_lower_leg_link">
        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
    </link>
    <link name="rh_foot_link">
        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 
    </link>
    <joint name="tower_joint" type="fixed">
        <origin xyz="0.0056 0.0068 0.10042" rpy="0 0 0"/>
        <parent link="base_link"/>
        <child link="tower_link"/>
    </joint>
    <joint name="f_bumper_joint" type="fixed">
        <origin xyz="0.1203 0.0000 -0.0042" rpy="0 0 0"/>
        <parent link="base_link"/>
        <child link="f_bumper_link"/>
    </joint>
    <joint name="h_bumper_joint" type="fixed">
        <origin xyz="-0.1199 0.0000 -0.0042" rpy="0 0 0"/>
        <parent link="base_link"/>
        <child link="h_bumper_link"/>
    </joint>
    <joint name="lf_hip_joint" type="revolute">
        <origin xyz="0.1105 0.0716 0.0009" rpy="0 0 0"/>
        <parent link="base_link"/>
        <child link="lf_hip_link"/>
        <axis xyz="1 0 0"/>
        <limit lower="-0.8726" upper="0.8726" effort="25" velocity="1.5"/>
    </joint>
    <joint name="lf_upper_leg_joint" type="revolute">
        <origin xyz="0.0000 0.0355 0.0041" rpy="0 0 0"/>
        <parent link="lf_hip_link"/>
        <child link="lf_upper_leg_link"/>
        <axis xyz="0 1 0"/>
        <limit lower="-1.0472" upper="1.0472" effort="25" velocity="1.5"/>
    </joint>
    <joint name="lf_lower_leg_joint" type="revolute">
        <origin xyz="0.0002 0.0003 -0.1078" rpy="0 0 0"/>
        <parent link="lf_upper_leg_link"/>
        <child link="lf_lower_leg_link"/>
        <axis xyz="0 1 0"/>
        <limit lower="-2.0944" upper="-1.0472" effort="25" velocity="1.5"/>
    </joint>
    <joint name="lf_foot_joint" type="fixed">
        <origin xyz="-0.0093 -0.0003 -0.1060" rpy="0 0 0"/>
        <parent link="lf_lower_leg_link"/>
        <child link="lf_foot_link"/>
    </joint>
    <joint name="rf_hip_joint" type="revolute">
        <origin xyz="0.1105 -0.0716 0.0009" rpy="0 0 0"/>
        <parent link="base_link"/>
        <child link="rf_hip_link"/>
        <axis xyz="1 0 0"/>
        <limit lower="-0.8726" upper="0.8726" effort="25" velocity="1.5"/>
    </joint>
    <joint name="rf_upper_leg_joint" type="revolute">
        <origin xyz="0.0000 -0.0355 0.0041" rpy="0 0 0"/>
        <parent link="rf_hip_link"/>
        <child link="rf_upper_leg_link"/>
        <axis xyz="0 1 0"/>
        <limit lower="-1.0472" upper="1.0472" effort="25" velocity="1.5"/>
    </joint>
    <joint name="rf_lower_leg_joint" type="revolute">
        <origin xyz="0.0002 -0.0003 -0.1078" rpy="0 0 0"/>
        <parent link="rf_upper_leg_link"/>
        <child link="rf_lower_leg_link"/>
        <axis xyz="0 1 0"/>
        <limit lower="-2.0944" upper="-1.0472" effort="25" velocity="1.5"/>
    </joint>
    <joint name="rf_foot_joint" type="fixed">
        <origin xyz="-0.0093 -0.0003 -0.1060" rpy="0 0 0"/>
        <parent link="rf_lower_leg_link"/>
        <child link="rf_foot_link"/>
    </joint>
    <joint name="lh_hip_joint" type="revolute">
     <origin xyz="-0.1131 0.0716 0.0009" rpy="0 0 0"/>
        <parent link="base_link"/>
        <child link="lh_hip_link"/>
        <axis xyz="1 0 0"/>
        <limit lower="-0.8726" upper="0.8726" effort="25" velocity="1.5"/>
    </joint>
    <joint name="lh_upper_leg_joint" type="revolute">
       <origin xyz="0.0000 0.0355 0.0041" rpy="0 0 0"/>
        <parent link="lh_hip_link"/>
        <child link="lh_upper_leg_link"/>
        <axis xyz="0 1 0"/>
        <limit lower="-1.0472" upper="1.0472" effort="25" velocity="1.5"/>
    </joint>
    <joint name="lh_lower_leg_joint" type="revolute">
       <origin xyz="0.0002 0.0003 -0.1078" rpy="0 0 0"/>
        <parent link="lh_upper_leg_link"/>
        <child link="lh_lower_leg_link"/>
        <axis xyz="0 1 0"/>
        <limit lower="-2.0944" upper="-1.0472" effort="25" velocity="1.5"/>
    </joint>
    <joint name="lh_foot_joint" type="fixed">
        <origin xyz="-0.0093 -0.0003 -0.1060" rpy="0 0 0"/>
        <parent link="lh_lower_leg_link"/>
        <child link="lh_foot_link"/>
    </joint>
    <joint name="rh_hip_joint" type="revolute">
      <origin xyz="-0.1131 -0.0716 0.0009" rpy="0 0 0"/>
        <parent link="base_link"/>
        <child link="rh_hip_link"/>
        <axis xyz="1 0 0"/>
        <limit lower="-0.8726" upper="0.8726" effort="25" velocity="1.5"/>
    </joint>
    <joint name="rh_upper_leg_joint" type="revolute">
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

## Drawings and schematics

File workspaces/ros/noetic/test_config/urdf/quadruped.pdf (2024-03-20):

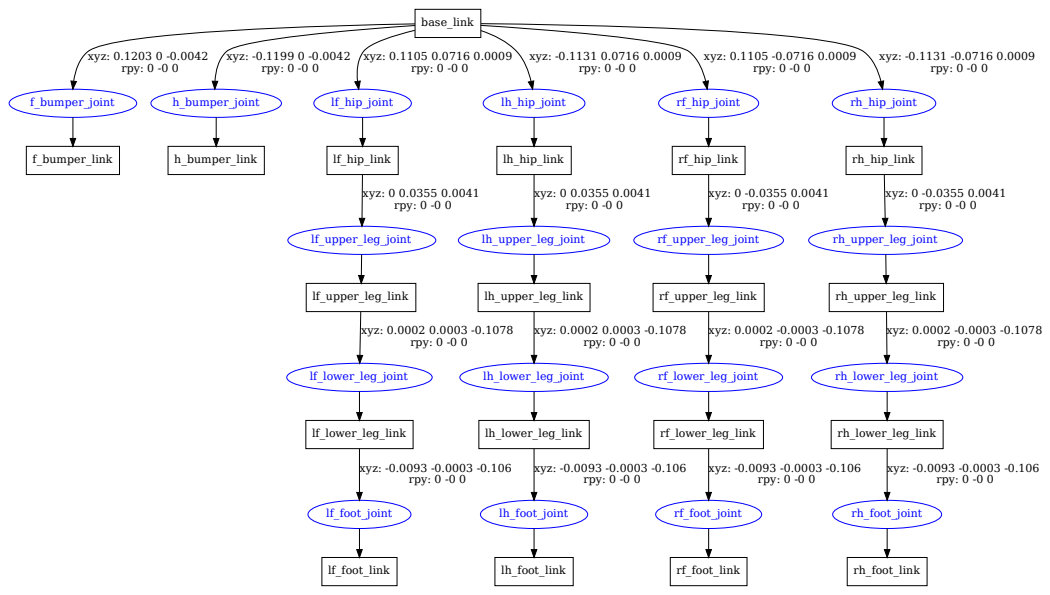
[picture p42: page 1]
base_link; f_bumper_joint; xyz: 0.1203 0 -0.0042 rpy: 0 -0 0; h_bumper_joint; xyz: -0.1199 0 -0.0042 rpy: 0 -0 0; lf_hip_joint; xyz: 0.1105 0.0716 0.0009 rpy: 0 -0 0; lh_hip_joint; xyz: -0.1131 0.0716 0.0009 rpy: 0 -0 0; rf_hip_joint; xyz: 0.1105 -0.0716 0.0009 rpy: 0 -0 0; rh_hip_joint; xyz: -0.1131 -0.0716 0.0009 rpy: 0 -0 0; f_bumper_link; h_bumper_link; lf_hip_link; lf_upper_leg_joint; xyz: 0 0.0355 0.0041 rpy: 0 -0 0; lf_upper_leg_link; lf_lower_leg_joint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

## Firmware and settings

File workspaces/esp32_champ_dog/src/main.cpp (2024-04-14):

#include "Config.h"
#include <Arduino.h>
#include <std_msgs/String.h>
#include <map>
#include "ros.h"
#include "champ_topics.h"
#include "pwm_servo.h"
#include "mpu_9250.h"
#ifdef ENABLE_WIFI
#include <WiFi.h>
IPAddress ip;
#endif
ros::NodeHandle nh;
PWM_Servo Servo;
MPU_9250 mpu;

void joint_trajectory_callback(const trajectory_msgs::JointTrajectory &msg)
{
  if (msg.points_length > 0)
  {
    for (int i = 0; i < msg.joint_names_length; i++)
    {
      Servo.update_pwm(msg.joint_names[i], msg.points[0].positions[i]);
    }
  }
}

void handleMsgs()
{
  static u_int64_t curr = millis(), prev = 0;
  if ((curr = millis()) - prev > 25)
  {
    prev = curr;
    champ_imu = mpu.composeMsg();
    champ_imu.header.stamp = nh.now();
    imu_pub.publish(&champ_imu);
  }
}

void setup()
{
  // put your setup code here, to run once:
#ifdef ENABLE_WIFI
  Serial.begin(115200);
  WiFi.begin("iinnii", "qwerasdf");
  while (!WiFi.isConnected())
  {
    Serial.println(WiFi.status());
  }
  ip.fromString(ROS_SERIAL_IP);
  nh.getHardware()->setConnection(ip, ROS_SERIAL_PORT);
#else
#ifdef USE_BLUETOOTH
  Serial.begin(115200);
#else
  Serial2.begin(115200);
  nh.getHardware()->setBaud(1000000);
#endif
#endif
  nh.initNode();
  // TODO: new function
  nh.subscribe(joint_trajectory_sub);
  nh.advertise(imu_pub);
  Servo.begin_hw();
  mpu.begin_hw();
}

void loop()
{
  // put your main code here, to run repeatedly:
  mpu.spinOnce();
  handleMsgs();
  nh.spinOnce();
}

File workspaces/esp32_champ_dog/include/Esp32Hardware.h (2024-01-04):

/* 
 * Software License Agreement (BSD License)
 *
 * Copyright (c) 2011, Willow Garage, Inc.
 * All rights reserved.
 *
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
 *  * Redistributions of source code must retain the above copyright
 *    notice, this list of conditions and the following disclaimer.
 *  * Redistributions in binary form must reproduce the above
 *    copyright notice, this list of conditions and the following
 *    disclaimer in the documentation and/or other materials provided
 *    with the distribution.
 *  * Neither the name of Willow Garage, Inc. nor the names of its
 *    contributors may be used to endorse or promote prducts derived
 *    from this software without specific prior written permission.
 *
 * THIS SOFTWARE IS PROVIDED BY THE COPYRIGHT HOLDERS AND CONTRIBUTORS
 * "AS IS" AND ANY EXPRESS OR IMPLIED WARRANTIES, INCLUDING, BUT NOT
 * LIMITED TO, THE IMPLIED WARRANTIES OF MERCHANTABILITY AND FITNESS
 * FOR A PARTICULAR PURPOSE ARE DISCLAIMED. IN NO EVENT SHALL THE
 * COPYRIGHT OWNER OR CONTRIBUTORS BE LIABLE FOR ANY DIRECT, INDIRECT,
 * INCIDENTAL, SPECIAL, EXEMPLARY, OR CONSEQUENTIAL DAMAGES (INCLUDING,
 * BUT NOT LIMITED TO, PROCUREMENT OF SUBSTITUTE GOODS OR SERVICES;
 * LOSS OF USE, DATA, OR PROFITS; OR BUSINESS INTERRUPTION) HOWEVER
 * CAUSED AND ON ANY THEORY OF LIABILITY, WHETHER IN CONTRACT, STRICT
 * LIABILITY, OR TORT (INCLUDING NEGLIGENCE OR OTHERWISE) ARISING IN
 * ANY WAY OUT OF THE USE OF THIS SOFTWARE, EVEN IF ADVISED OF THE
 * POSSIBILITY OF SUCH DAMAGE.
 */
#ifndef ROS_ARDUINO_HARDWARE_H_
#define ROS_ARDUINO_HARDWARE_H_

#if ARDUINO >= 100
#include <Arduino.h> // Arduino 1.0
#else
#include <WProgram.h> // Arduino 0022
#endif

#if defined(__MK20DX128__) || defined(__MK20DX256__) || defined(__MK64FX512__) || defined(__MK66FX1M0__) || defined(__MKL26Z64__) || defined(__IMXRT1062__)
#if defined(USE_TEENSY_HW_SERIAL)
#define SERIAL_CLASS HardwareSerial // Teensy HW Serial
#else
#include <usb_serial.h> // Teensy 3.0 and 3.1
#define SERIAL_CLASS usb_serial_class
#endif
#elif defined(_SAM3XA_)
#include <UARTClass.h> // Arduino Due
#define SERIAL_CLASS UARTClass
#elif defined(USE_USBCON)
// Arduino Leonardo USB Serial Port
#define SERIAL_CLASS Serial_
#elif (defined(__STM32F1__) and !(defined(USE_STM32_HW_SERIAL))) or defined(SPARK)
// Stm32duino Maple mini USB Serial Port
#define SERIAL_CLASS USBSerial
#elif defined(USE_BLUETOOTH)
#include <BluetoothSerial.h>
#if !defined(CONFIG_BT_ENABLED) || !defined(CONFIG_BLUEDROID_ENABLED)
#error Bluetooth is not enabled! Please run `make menuconfig` to and enable it
#endif

#if !defined(CONFIG_BT_SPP_ENABLED)
#error Serial Bluetooth not available or not enabled. It is only available for the ESP32 chip.
#endif
static BluetoothSerial bluetoothSPP;
#define SERIAL_CLASS BluetoothSerial
void BTConfirmRequestCallback(uint32_t numVal){
  bluetoothSPP.confirmReply(true);
}
#else
#include <HardwareSerial.h> // Arduino AVR
#define SERIAL_CLASS HardwareSerial
#endif

class ArduinoHardware
{
public:
  ArduinoHardware(SERIAL_CLASS *io, long baud = 1500000)
  {
    iostream = io;
    baud_ = baud;
  }
  ArduinoHardware()
  {
#if defined(USE_BLUETOOTH)
    iostream = &bluetoothSPP;
#else
    iostream = &Serial;
#endif
    baud_ = 1500000;
  }
  ArduinoHardware(ArduinoHardware &h)
  {
    this->iostream = h.iostream;
    this->baud_ = h.baud_;
  }

  void setPort(SERIAL_CLASS *io)
  {
    this->iostream = io;
  }

  void setBaud(long baud)
  {
    this->baud_ = baud;
  }

  int getBaud() { return baud_; }

  void init()
  {
#if defined(USE_BLUETOOTH)
    uint64_t chipid = ESP.getEfuseMac();
    String id = String((uint16_t)(chipid >> 32), HEX);
    id.toUpperCase();
    // iostream->setPin("2345");
    // iostream->enableSSP(); // Must be called before begin
    iostream->onConfirmRequest(BTConfirmRequestCallback);
    iostream->begin("KKY-" + id);
#else
#if defined(USE_USBCON)
    // Startup delay as a fail-safe to upload a new sketch
    delay(3000);
#endif
    iostream->begin(baud_);
#endif
  }

  int read()
  {
#if defined(USE_BLUETOOTH)
    if (iostream->connected())
    {
      return iostream->read();
    }
    else
    {
      return -1;
    }
#else
    return iostream->read();
#endif
  }
  void write(uint8_t data)
  {
    iostream->write(data);
  }
  void write(const uint8_t *data, int length)
  {
    iostream->write(data, length);
  }

  unsigned long time() { return millis(); }

protected:
  SERIAL_CLASS *iostream;
  long baud_;
};

#endif

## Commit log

2023-06-18 Initial commit. Added custom bluetooth controller. Need dog calibration.
2023-06-22 feat: dog calibration (in progress). cli for bluebooth connection.
2023-06-28 feat: calibrating
2023-06-30 more calibrating
2023-07-02 feat: calibration calculator. (need testing)
2023-07-06 feat: calibration parser v1.
2023-10-23 feat: tested joint_state topic.
2023-11-07 feat: custom champ packages
    [controllers.yaml, quadruped.urdf, ros_control.yaml]
2023-11-07 feat: servo firmware (temp commit)
2023-11-14 feat: servo integration
2023-11-17 feat: configured angle & pwm constraints
2023-11-17 feat: added timer callback for hw controller
    [controllers.yaml]
2023-12-01 feat: champ-pkg update
    [controllers.yaml, quadruped.urdf, ros_control.yaml]
2023-12-15 doc: added information for lidar and 3d modeling.
    [body-bottom.stl, body-bumper.stl, body-top.stl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]
2023-12-19 feat: ros control imu
    [controllers.yaml, quadruped.urdf, ros_control.yaml]
2023-12-21 fix: orientation message. progress: leg calibration.
    [body-bottom.stl, quadruped.urdf, shoulder-joint-left.stl]
2023-12-26 feat: update README.md for lidar module
2023-12-28 feat: added error values to imu message. fix: tuned bluetooth buffer values. refactor: main loop
    [BluetoothSerial.cpp, main.cpp]
2023-12-28 feat: add blends file and update meshes for urdf
    [body-bottom.stl, body.blend, body.stl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]
2023-12-28 feat: update part names and modify bringup.launch
    [base.blend, base.stl, body.blend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]
2023-12-29 fix: update the orientation of base model
    [base.blend, base.stl]
2023-12-29 feat: added accel offset "calibration"
2023-12-30 feat: create quadruped.urdf.xacro and update blender files
    [base.blend, base.stl, bumper.blend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]
2023-12-30 sbc header
    [small_sbc_header.stl]
2023-12-31 modified sbc header
    [refined_sbc_header.stl]
2024-01-02 feat: update joint positions in urdf
    [quadruped.urdf.xacro]
2024-01-03 feat: update joints' constraints and configurations
    [quadruped.urdf.xacro]
2024-01-03 feat: update urdf file
    [quadruped.urdf.xacro]
2024-01-04 feat: first calibration of dog. fix: move node spin to loop(). refactor: imu callback in ros controller.
    [BluetoothSerial.cpp, Esp32Hardware.h, gait.yaml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]
2024-03-20 refactor: docker compose
    [accessories.urdf.xacro, base.stl, bumper.stl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]
2024-03-21 fix: use pwm servo offset header
2024-03-23 feat: pid on pitch and roll from imu
    [pid.yaml]
2024-03-26 feat: tuned balancing
    [pid.yaml]
2024-04-05 feat: added camera urdf. Modified servo pins.
    [_d415.urdf.xacro, _d435.urdf.xacro, _d435i.urdf.xacro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]
2024-04-08 Feat/urdf viewer (#8)
    * feat: added 3D visualization for robot. Refactored router and ros context.
    [base.stl, bumper.stl, d455.stl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]
2024-04-09 feat: passthrough ttyUSB0 to bridge esp32 connection
2024-04-09 try cameracontrol
2024-04-10 fix: pwm calibration
2024-04-11 feat: balance mode trigger
    [pid.yaml]
2024-04-14 feat: added camera feed. updated hw.
2024-04-14 feat: add tower component to urdf
    [base.blend, base.stl, quadruped.urdf.xacro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]
2024-04-14 feat: generate the urdf file from xacro
    [quadruped.urdf]
2024-04-14 feat: mesh for newviz.
    [base.stl, quadruped.urdf, tower.stl]
2024-04-14 fix: update z offset of camera_link
    [quadruped.urdf, quadruped.urdf.xacro]
2024-04-15 feat: update ekf config to fuse imu data
2024-04-20 fix: signup.jsx added msg after button click
2024-04-27 feat: reorganise project folder structure
    [_d415.urdf.xacro, _d435.urdf.xacro, _d435i.urdf.xacro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]
2024-04-27 fix: add software requirements for Jetson
